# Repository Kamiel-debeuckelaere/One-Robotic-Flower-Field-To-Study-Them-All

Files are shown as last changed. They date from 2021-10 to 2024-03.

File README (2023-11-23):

Dear visitor

In this repository you can find several folders, each containing different information and files to construct robotic flowers.
- 3D-design files
- Firmware to put on the arduino (only use one of the two included .cpp files!)
- Node-RED flows
- PCB-design files
- Proof of concept, with data, script and video

We bundled a lot of information in the user manual, including instructions for construction and use of the robotic flower. 
I hope you can find everything you need, if not, don't hesitate to ask!

Kind regards

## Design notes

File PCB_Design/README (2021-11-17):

This folder contains files to obtain Gerber files that are needed for PCB fabrication. 
Open these files in EasyEDA online.

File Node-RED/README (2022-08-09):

This directory contains 2 flows in JSON format that can be imported in Node-RED.
More information on how to import a flow: https://nodered.org/docs/user-guide/editor/workspace/import-export

These flows construct the dashboard website (see figure) and construct the CSV files of incoming data.

It is necessary to add the following modules to the palette:
- node-red-contrib-fs
- node-red-dashboard
- node-red-node-tail

The 'File Logger Flow' is only needed once per robotic flower field system.
-> change path to folder where CSV should be stored (nodes: 'filename generator', 'file-lister', 'init' and 'reset')

The 'Flower Flow' is needed for every separate robotic flower in the system
-> change topic so it contains the right device and app name!
-> update server security settings in downlink and uplink node for each flower
-> create dashboard website tabs (Battery, Alarms, Sleep time, Refill gap and Files) and groups for each flower
-> next, assign the following nodes per flower to the right tab and group, an example for flower 1:
    - Received: '[Alarms] Flower1' 
    - Received: '[Battery] Flower1' 
    - Chart:'[Battery] Flower1' 
    - Gauge: '[Battery] Flower1' 
    - Queue is full: '[Alarms] Flower1' 
    - Send during visit: '[Alarms] Flower1' 
    - Battery warning: '[Alarms] Flower1' 
    - Possible obstruction: '[Alarms] Flower1'
    - Refill gap: '[Refill gap] Flower1' 
    - Going to sleep at: '[Sleep time] Flower1'
    - Waking up at: '[Sleep time] Flower1' 

Screenshots of dashboard website
The user interface of the frontend application with the different tabs opened. 
For example, in the 'battery' tab an overview of all the robotic flowers in use can be seen with the time of the last update (last received message), 
the battery voltage, and a graph of the voltage decline in function of time.

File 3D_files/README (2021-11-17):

This directory contains a Zip-compressed archive file for Autodesk® Fusion 360® (.f3z) and a folder with stl-files of the prototype ready for 3D-printing.

To open the archive file, select "Upload" in the Fusion 360 Data panel and choose the F3Z file. 
The contents of the file will be loaded in Fusion 360, displaying the main assembly in the panel with the F3D design(s), allowing you to view and edit them.

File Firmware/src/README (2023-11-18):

In this folder, there are 4 possible sourcefiles containing a slightly different program. 

!! you can only use one source file at once, so delete the ones you don't need before opening the 'firmware' folder in e.g., Visual Studio Code !!
 
 1) 'main.cpp' has automatic refilling and a refill gap (that can be chosen from the NodeRed dashboard website) after a visit,
     keep in mind you have to slect a refill gap in orde to have the flower working properly!
 
 2) 'main_autoRefillOnly.cpp' only has the automatic refilling (that can be chosen from the NodeRed dashboard website)

 3) 'main_no_sending.cpp' can be selected if you want to use the robotic flower for refilling only

 4) 'main_RFID_no_RX_sending.cpp' can be selected when you combine the flowers with the Microsensys RFID system.
     The RFID radio waves will make the flowers deaf, meaning they cannot receive instructions anymore, so in this firmware version,
     when the flower is put to sleep, it will keep sending data but not expecting an answer. Note that you will have to put the
     flowers to sleep from the dashboard website before switching on the RFID readers.

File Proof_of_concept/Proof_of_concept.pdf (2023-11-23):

# Proof of concept

## Contents

## 1. First tests

A proof of concept was performed to test whether the robotic flower does what it was designed to do. Multiple insects in different settings were used on July 16, 2021. The question was if the robotic flowers could attract visitors by offering artificial nectar and if so, correctly register the visit data. Therefore, the CSV-file with visit data of the robotic flower had to be compared to the manually collected visit time and visit duration. Two robotic flowers were used of which the nectar reservoir was filled with Biogluc (50% w/w) sugar syrup (composed of 25.0% sucrose, 37.5% fructose, 34.5% dextrose, 2.0% maltose, 1% higher sugars and 0.05% preservatives) made by Biobest (Billiet et al., 2016).

## 1.1 Open Field

As a first setting, the robotic flower was placed in the garden. Floral visitors were recorded in an open field setting, being a small botanical garden. When the visitor went in the feeding hole, the probing time and duration were noted (table 1). The captured individuals were identified and besides Bombus terrestris, also B. pascuorum, Anthidium manicatum, Apis mellifera, Psythirus sp., Syrphidae, Bombyliidae and even one Lepidopteran showed interest in the robotic flower (at least to a certain extent). After manually registering visits, we compared this to the data collected by the robotic flower. 7 out of the 10 visitors that actually went in the feeding hole to drink were recorded by the robotic flower, but we noticed that some visits were not or only partly recorded (See table 1). In retrospect, this could be partly explained by the ‘SENSOR_SENSITIVITY’ value that was used. The sensitivity of the IR detection system, that was set at a good value for the breadboard prototype, might have been insufficient sensitive in the garden conditions, especially for the smaller floral visitors. For butterflies, with their long proboscis, a more refined feeding hole would probably be needed to get sufficient blocking of the infrared sensor.

2

## Table 1

Manual measurement | Robotic Flower | Analysis Robotic Flower system
Species | Class | Remarks

Visit Time
(hh:mm)

Visit
Duration (s)

Visit Time
(hh:mm:ss)

Visit
Duration (s) Visit registration | Percentage time
1 | Syrphidae | Fly | | 13:33 | 8 | | | x
2 | Bombus pascuorum | Bee | male | 13:45 | 5 | | | x
3 | Bombyliidae | Fly | | 14:08 | 240 | 14:08:49 | 78 | Yes | 33%
4 | Lepidoptera | Butterfly | | 14:13 | 158 | | | x
5 | Bombus pascuorum | Bee | didn’t drink | 14:19
6 | Syrphidae | Fly | didn’t drink | 14:22
7 | Anthidium manicatum | Bee | | 14:59 | | 14:59:17 | 2 | Yes
8 | Bombyliidae | Fly | didn’t drink | 15:11
9 | Apis mellifera | Bee | didn’t drink | 15:23
10 | Apis mellifera | Bee | 2nd visit by same bee | 15:39 | 35 | 15:39:23 | 26 | Yes | 74%
11 | Apis mellifera | Bee | 3th visit by same bee | 15:39 | 10 | 15:40:01 | 14 | Yes | 140%
12 | Apis mellifera | Bee | | 15:49 | 8 | 15:49:20 | 3 | Yes | 38%
13 | Bombus terrestris | Bee | | 15:51 | 148 | 15:51:26 | 52 | Yes | 35%
14 | Bombus terrestris | Bee | male | 15:56 | 9 | 15:57:20 | 9 | Yes | 100%

## 2.1 Greenhouse

The second setting was in the greenhouse with the robotic flower placed inside a small flight cage (60 × 60 × 60 cm; front and back in clear vinyl, right and left in polyester netting mesh, Bugdorm, Megaview Ltd.; Fig. 1) together with lab-reared floral visitors from Biobest (Westerlo, Belgium). Two species were tested in separate trials: bumble bees (Bombus terrestris), and Eupeodes corollae (a common European species of Syrphidae). After a training period, both speciesshowed great interest in the robotic flower, making it sometimes hard to visually discriminate multiple visits. That is most likely why the results of the manual data collection often show only one visit where the robotic flower recorded multiple visits (Table 2). All visits detected manually were also present in the data sent by the robotic flower.

The robotic flower has a visit time accurate to the second while the manual registration only had minutes, but the visit times seem to match perfectly, as can be seen in Table 2. The ‘duration overlap’ gives a view on the difference between manual and the robotic measurement of the visit duration (the separate robotic flower timings added together and divided by the manual timing). This was close to 100% in many cases, and the deviations can be explained in different ways. A duration overlap is different from 100% could be the effect of multiple visits that were measured by the robotic flower compared to one large visit in the manual censuses. The small gaps in between these visits can explain the difference in visit duration. For example, in visit 5 in the flight cage setup (Table 2), the manual measurement shows one long visit of 77 seconds, while the robotic flower registered five different visits of 9, 5, 4, 12 and 27 seconds. The total of the three separate visits gives a duration of 57 seconds, which means a duration overlap of 74%. When looking closer to the intervals between those visits, we see gaps of 2, 5, 1 and 12 seconds. Taking these
gaps into account, the result is a duration of
77 seconds and thus a duration overlap of
100%. In visits with a small duration, the duration overlap can drastically deviate from the target value of 100% because of manual registration bias. Starting or stopping the timer a fraction later or earlier and rounding errors by the observer has a big impact if the visit duration was only a couple of seconds. For example, visit 19 (Table 2) had a manual measured duration of only 2 seconds, while the robotic flower registered 3 seconds. Only one second difference in this case leads to a duration overlap percentage of 150%.

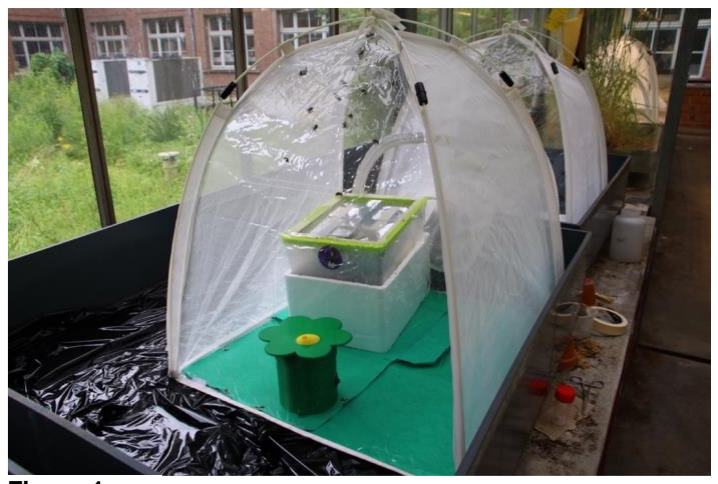
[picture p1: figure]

Looking critically at the results of the analysis of the robotic flower, it can be concluded that the detection of visits works as it should, provided that the IR sensitivity is set to the right value for the setup. A calibration is thus recommended before starting an experiment using the robotic flowers. This proof of concept also showed that not only bumble bees but also many other floral visitors can be investigated even with the same hardware parts. In the set-up with the flight cage, we had satisfactory results for the syrphids E. corollae although it is advisable to reduce the diameter of the feeding hole specifically to better match their body size.

Figure 1

4

## Table 2

Manual Measurement | Robotic Flower | Analysis Robotic Flower system
Species | Visit Time (hh:mm) | Visit Duration (s) | Visit Time (hh:mm:ss) | Visit Duration (s) | Visit registration | Duration overlap (%)
B. terrestris | 15:18 | 128 | 15:18:16 | 51 | Yes | 98%
| | | 15:19:09 | 52
| | | 15:20:02 | 23
B. terrestris | 15:21 | 27 | 15:21:06 | 20 | Yes | 96%
| | | 15:21:38 | 6
B. terrestris | 15:22 | 67 | 15:22:04 | 3 | Yes | 93%
| | | 15:22:09 | 1
| | | 15:22:12 | 58
B. terrestris | 15:23 | 56 | 15:23:17 | 10 | Yes | 66%
| | | 15:23:30 | 12
| | | 15:23:51 | 15
B. terrestris | 15:24 | 77 | 15:24:09 | 9 | Yes | 74%
| | | 15:24:20 | 5
| | | 15:24:30 | 4
| | | 15:24:35 | 12

5

15:24:59 | 27
B. terrestris | 15:28 | 39 | 15:28:03 | 27 | Yes | 82%
| | | 15:28:39 | 5
B. terrestris | 15:33 | 26 | 15:33:54 | 22 | Yes | 104%
| | | 15:34:18 | 5
B. terrestris | 15:35 | 23 | 15:35:09 | 25 | Yes | 109%
B. terrestris | 15:35 | 9 | 15:35:48 | 3 | Yes | 33%
B. terrestris | 15:35 | 29 | 15:35:56 | 21 | Yes | 72%
B. terrestris | 15:37 | 13 | 15:37:03 | 9 | Yes | 69%
B. terrestris | 15:37 | 5 | 15:37:22 | 14 | Yes | 280%
B. terrestris | 15:37 | 14 | 15:37:44 | 12 | Yes | 100%
| | | 15:37:58 | 2
B. terrestris | 15:42 | 46 | 15:42:11 | 39 | Yes | 98%
| | | 15:42:52 | 6
B. terrestris | 15:43 | 7 | 15:43:05 | 30 | Yes | 125%
B. terrestris | 15:43 | 17
B. terrestris | 15:43 | 31 | 15:43:38 | 8 | Yes | 90%
| | | 15:43:48 | 2

6

15:43:56 | 18
B. terrestris | 15:44 | 47 | 15:44:49 | 37 | Yes | 79%
B. terrestris | 15:45 | 2 | 15:45:30 | 3 | Yes | 150%
B. terrestris | 15:46 | 5 | 15:46:00 | 1 | Yes | 140%
| | | 15:46:15 | 6
B. terrestris | 15:47 | 10 | 15:47:04 | 38 | Yes | 127%
B. terrestris | 15:47 | 20
E. corollae | 15:56 | 75 | 15:56:15 | 3 | Yes | 85%
| | | 15:56:53 | 13
| | | 15:57:41 | 30
| | | 15:58:17 | 18
E. corollae | 15:59 | 175 | 15:58:43 | 190 | Yes | 109%

## 2. Foraging-preference experiment

To further prove the value of this new robotic flower, we performed a bumblebee foraging-preference experiment with two reward qualities in a greenhouse setting. After training on less rewarding flowers, we expect an initial preference for these lower-quality flowers (flower constancy) with a gradual shift towards the higher quality option during the trial (Heinrich, 1981). To test this, a robotic flower field consisting of 16 robotic flowers, alternating less and more rewarding flowers in a 4x4 setup, was used in two subsequent replicate trials (Fig. 2). The two types of flowers are represented by different colours, yellow and blue, so that foragers can discriminate between them visually and associate them with reward quality (Hammer & Menzel, 1995). We used Biogluc 30% w/w (less rewarding) and 60% w/w (more rewarding) as artificial nectar with preservatives to reduce microbial growth (Billiet et al., 2016). For both trials, a 7-weeks old lab-reared B. terrestris colony was placed in the arena with the robotic flowers. Before a trial, colonies were fed pollen and Biogluc ad libitum directly in the nest, but Biogluc supply was ceased 24 hours in advance to stimulate foraging. A trial started with 36 hours of training, where the colony was placed in a closed bug dorm with two 30% w/w rewarding flowers (without refilling gap). Subsequently, the bug dorm was opened at night to allow foraging in the arena starting the next morning. A refill gap of 30 minutes was implemented during this experimental phase.

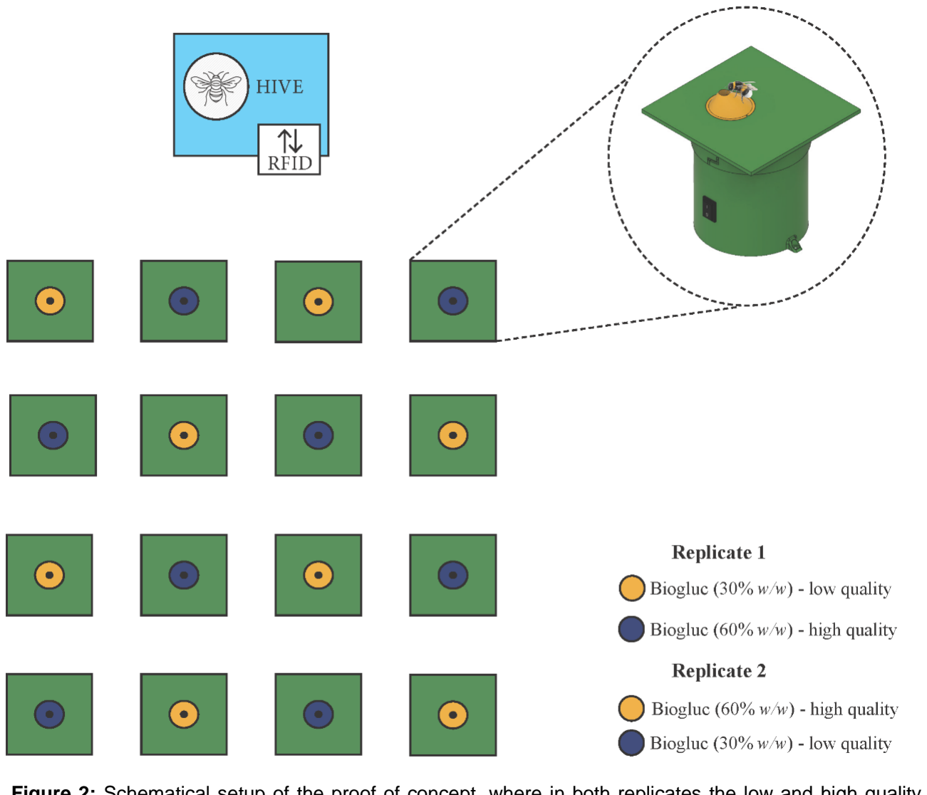
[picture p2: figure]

Figure 2: Schematical setup of the proof of concept, where in both replicates the low and high quality sources were switched between the yellow and blue flower.

In total, 70 177 visits were recorded in this proof of concept. During the daily inspection of the setup within peak activity time-slots, a maximum of five foragers at once were observed. with the earliest flower visit at 7:36 and the latest at 19:17, the natural light regime (sunrise ~7:55, sunset ~19:00) was well visible.

The data were analysed using R version 4.2.1 (R Core Team, 2022). A heatmap representing the number of visits per flower per treatment (Fig. 3) already indicates an initial preference for the low concentration flowers with a switch towards the high concentration during the experiment.

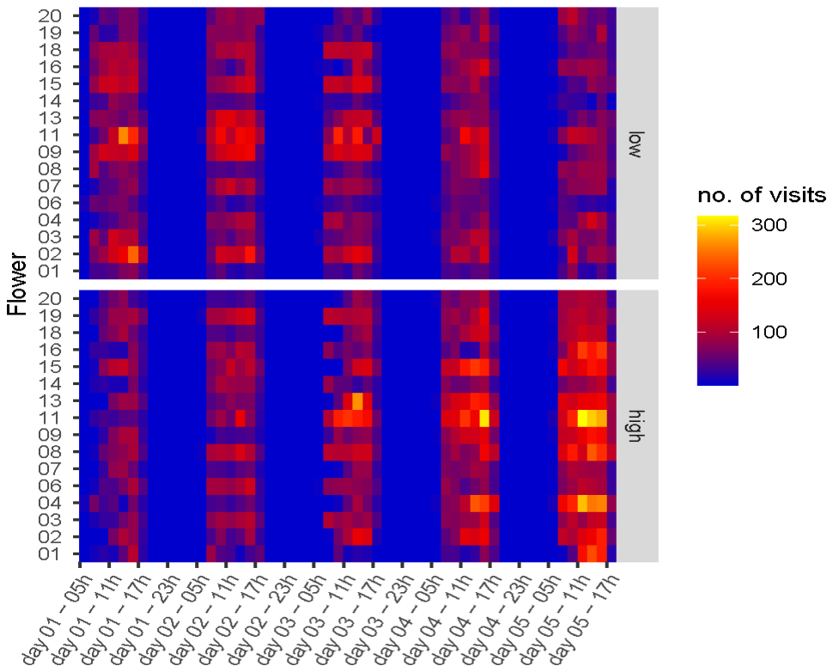
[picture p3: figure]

Data on the number of visits per hour per flower (n) were used in a general linear mixed model with Poisson distribution and an observation level random factor to account for overdispersion:

fit = glmer(n ~ (1|flower) + concentration * scale(exp_day) +

mSpline(hour_of_day, df=7, Boundary.knots = c(0,24), periodic=TRUE) + (1|obs),

family = poisson (link="log"), data = model_data,

control = glmerControl(optimizer = "Nelder_Mead", optCtrl = list(maxfun=100000)))

Figure 3: A heatmap of the number of flower visits per quality of the nectar reward over the experimental period.

As can be seen in the Anova table (table 3), the model gives a significant effect of experimental day (p = 0.00039), as well as a significant interaction between the Biogluc concentration and experimental day (p < 2.2e⁻¹⁶). A significant effect was also found for the circadian rhythm in foraging (p < 2.2e⁻¹⁶).

In the first day after being trained on the low concentration, bumblebees visit the low concentration flowers about double as much as they visit high concentration flowers (high/low contrast ratio = 0.525, p < 0.0001). There is a linear trend of increasingly more visits towards the high concentration compared to the low concentration (high/low contrast estimate = 0.338, p < 0.0001), resulting in no significant difference in visitation rate between the two concentrations on the third experimental day (high/low contrast ratio = 1.032, p = 0.2765). On the last experimental day, the preference has switched to little over double the amount of visits to high concentration flowers compared to the low concentration flowers (high/low contrast ratio = 2.030, p < 0.0001). The effect plot (Fig. 4) gives a clear view on this preference shift, including the circadian rhythm in foraging.

Table 3: Anova

Predictor | Chisq | Df | P value
Intercept | 47.28744 | 1 | 6.13E-12 ***
Concentration | 1.184415 | 1 | 0.276
Experimental day | 12.57797 | 1 | 0.00039 ***
Hour of day | 3205.677 | 7 | < 2.2E-16 ***
Conc. : Exp. Day | 265.8984 | 1 | < 2.2E-16 ***

Table 4: Estimated marginal means of linear trends (emtrends)

Contrast | Estimate | SE | P value
High/Low | 0.338 | 0.0207 | < 0.0001 ***

Table 5: Estimated marginal means (emmeans)

Contrast | Day | Ratio | SE | P value
High/Low | 1 | 0.525 | 0.0270 | < 0.0001 ***
High/Low | 2 | 0.736 | 0.0268 | < 0.0001 ***
High/Low | 3 | 1.032 | 0.0303 | 0.2765
High/Low | 4 | 1.448 | 0.0514 | < 0.0001 ***
High/Low | 5 | 2.030 | 0.1019 | < 0.0001 ***

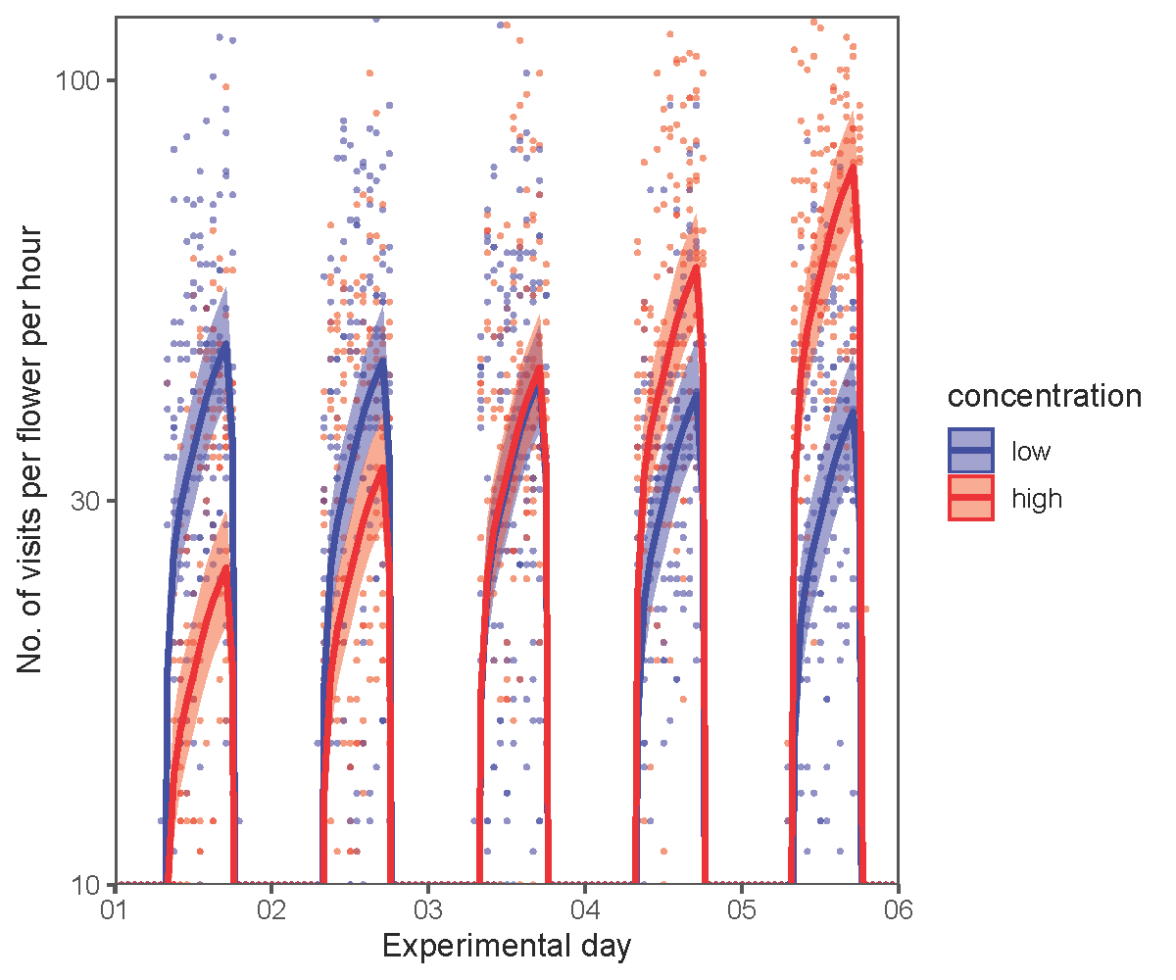
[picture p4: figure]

## 3. Waterproof testing

A robotic flower was put outside in rainy conditions (November 2023) to see if the system can withstand the water (Fig. 5). For this test, we used the roofed central flower disk design to prevent water entering the feeding hole. To make sure the flower bottom is not soaked completely in the wet underground, we elevated it slightly from the ground. To prevent tipping over by the wind or uncareful by passers (e.g. nosy birds), the flower was anchored in the ground.

The flower kept working as long as the battery was charged and did not show any signs of leakage, which proved the system’s water resistance.

Figure 4: An effect plot of the number of bumblebee flower visits per concentration as predicted by the generalized linear mixed model plotted over the raw data.

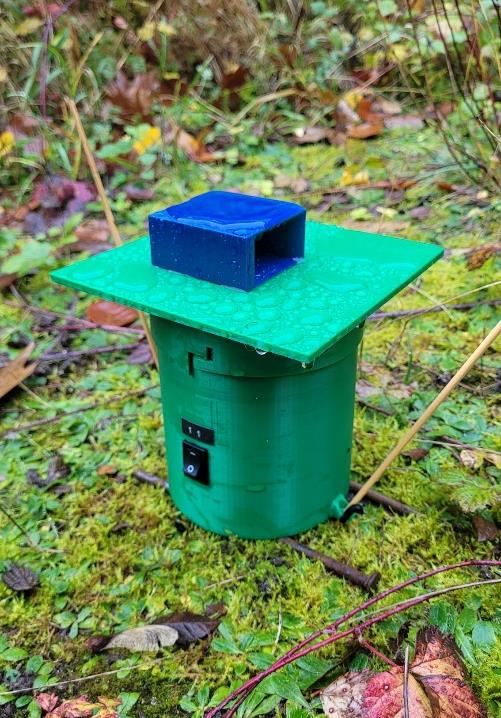
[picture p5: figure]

Figure 5: a robotic flower placed outside in the rain, anchored in the ground.

## 4. References

Billiet, A., Meeus, I., Van Nieuwerburgh, F., Deforce, D., Wackers, F., & Smagghe, G. (2016). Impact of sugar syrup and pollen diet on the bacterial diversity in the gut of indoor-reared bumblebees (Bombus terrestris). Apidologie, 47(4), 548-560. https://doi.org/10.1007/s13592-015-0399-1

Hammer, M., & Menzel, R. (1995). Learning and memory in the honeybee. The Journal of Neuroscience, 15(3), 1617-1630. https://doi.org/10.1523/jneurosci.15-03-01617.1995

Heinrich, B. (1981). Bumblebee economics (3 ed.). Harvard University Press.

R Core Team. (2022). R: A language and environment for statistical computing. In R Foundation for Statistical Computing. https://www.R-project.org/

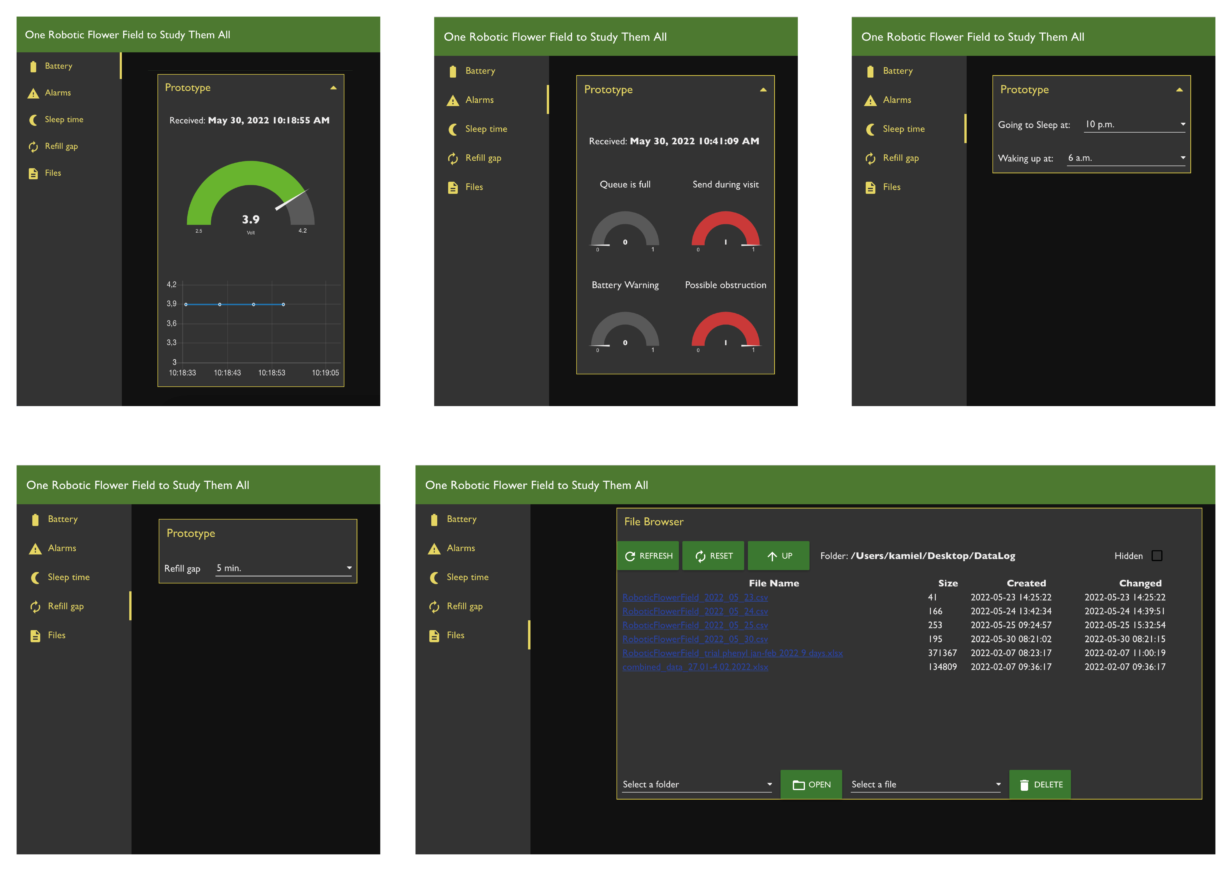
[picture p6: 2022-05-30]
Node-RED/dashboard view 2.png

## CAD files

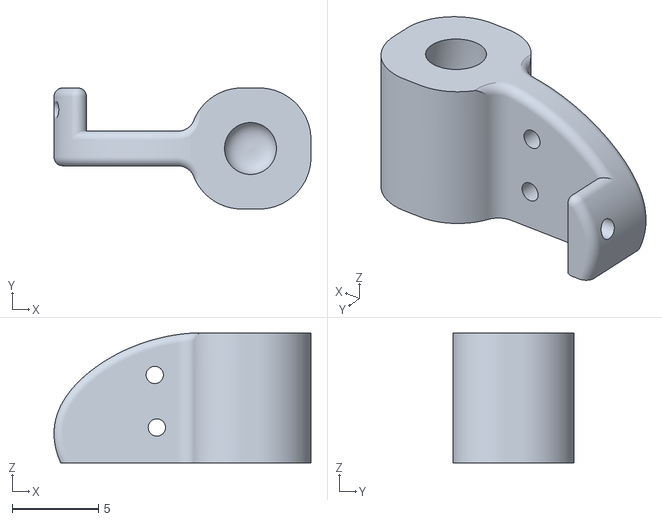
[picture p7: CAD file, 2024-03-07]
3D_files/Robotic_Flower_STL/Nectar cup 2 - 15 µL.stl
14.9 x 7.00 x 7.50

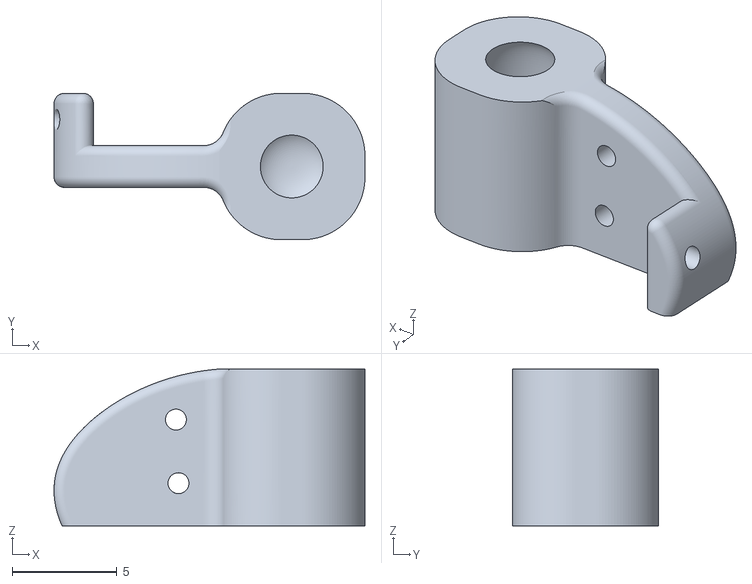
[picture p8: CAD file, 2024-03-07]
3D_files/Robotic_Flower_STL/Nectar cup 1 - 22 µL.stl
14.9 x 7.00 x 7.50

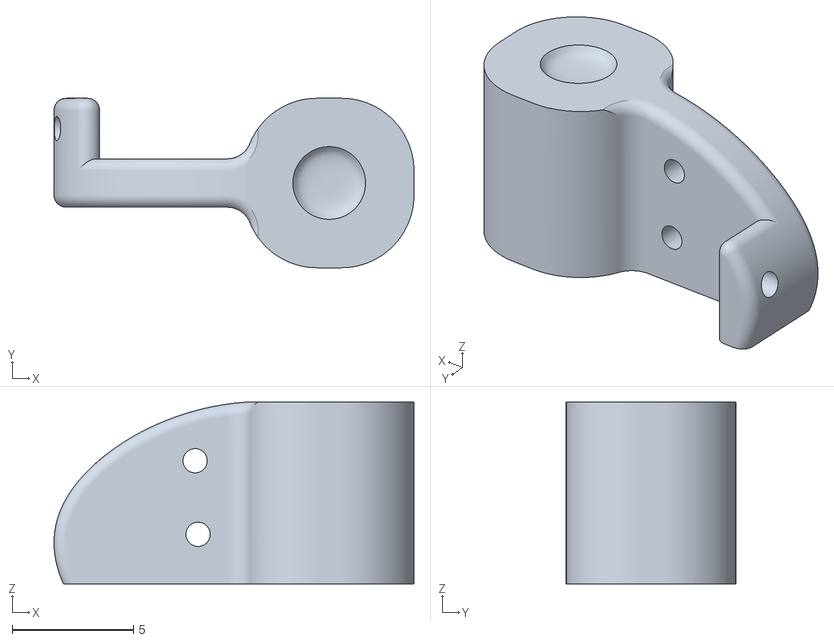
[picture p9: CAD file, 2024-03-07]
3D_files/Robotic_Flower_STL/Nectar cup 5 - 6.4 µL.stl
14.9 x 7.00 x 7.50

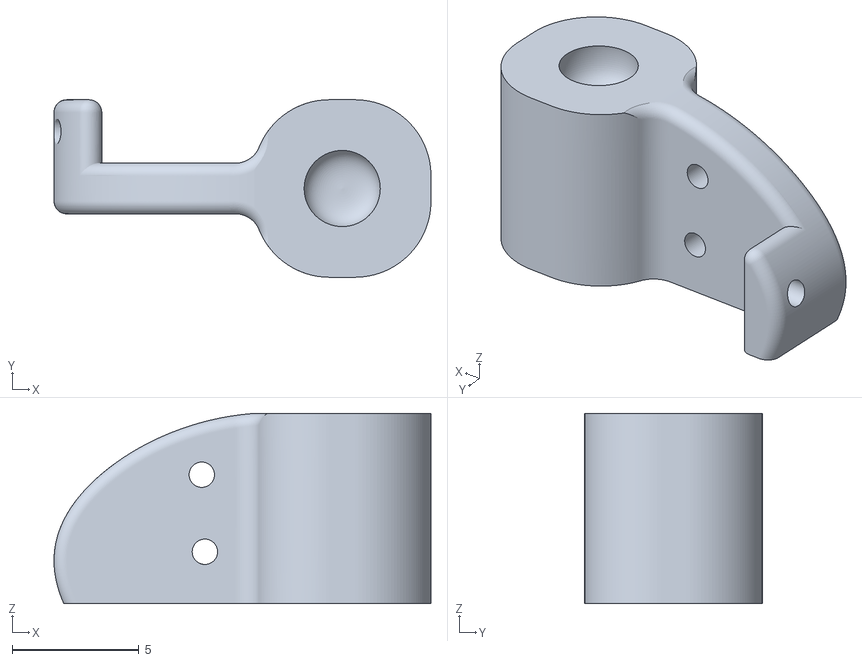
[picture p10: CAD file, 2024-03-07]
3D_files/Robotic_Flower_STL/Nectar cup 3 - 12 µL.stl
14.9 x 7.00 x 7.50

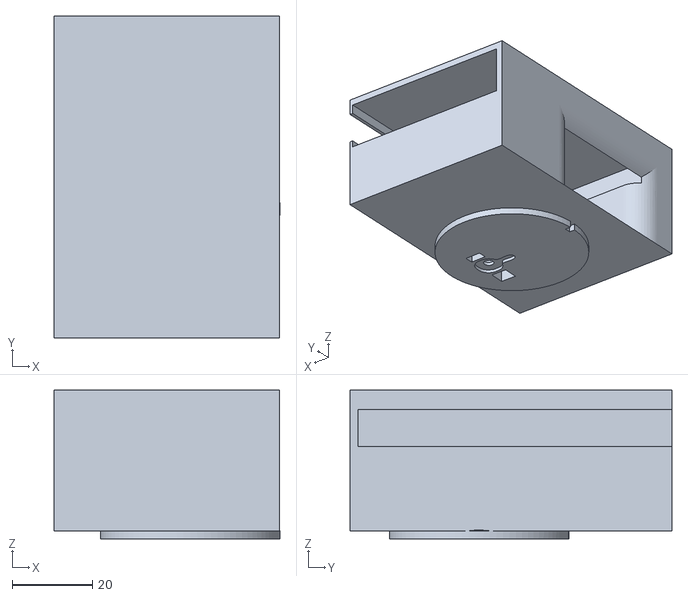
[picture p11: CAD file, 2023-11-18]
3D_files/Robotic_Flower_STL/Central flower disk - RFID.stl
56.2 x 80.0 x 37.0

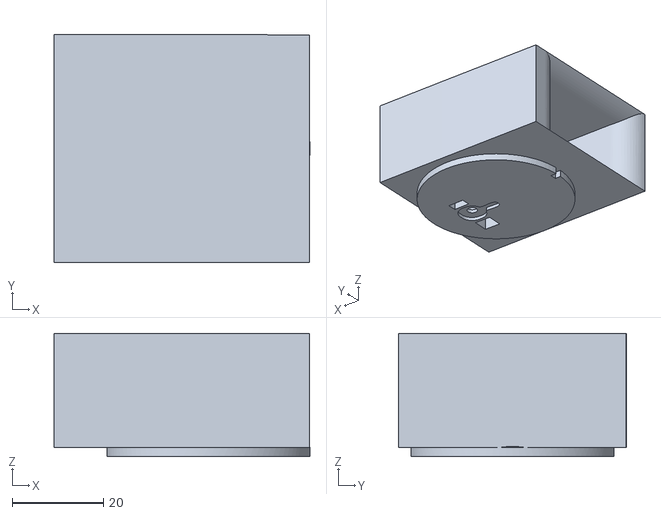
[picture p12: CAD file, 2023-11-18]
3D_files/Robotic_Flower_STL/Central flower disk - roof.stl
56.2 x 50.0 x 27.0

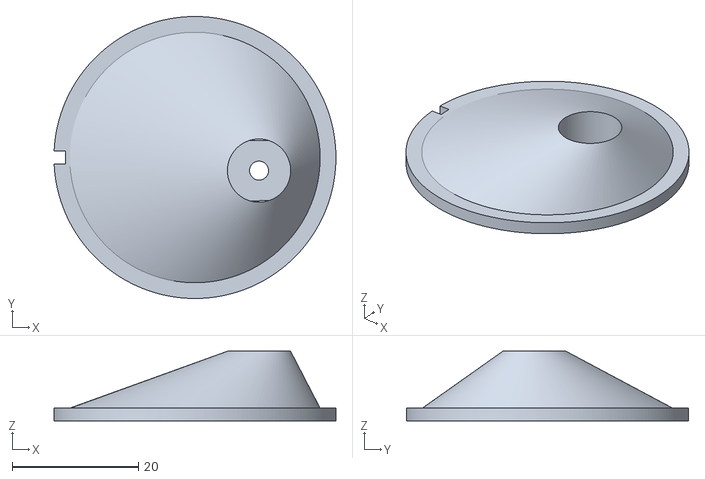
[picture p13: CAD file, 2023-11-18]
3D_files/Robotic_Flower_STL/Central flower disk - standard.stl
44.6 x 44.6 x 11.0

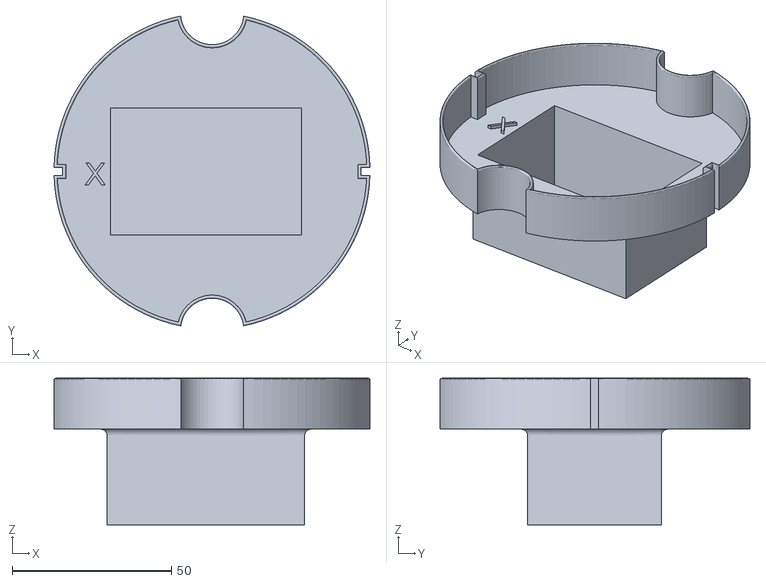
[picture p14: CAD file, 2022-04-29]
3D_files/Robotic_Flower_STL/Reservoir Case (black).stl
99.2 x 97.2 x 46.0

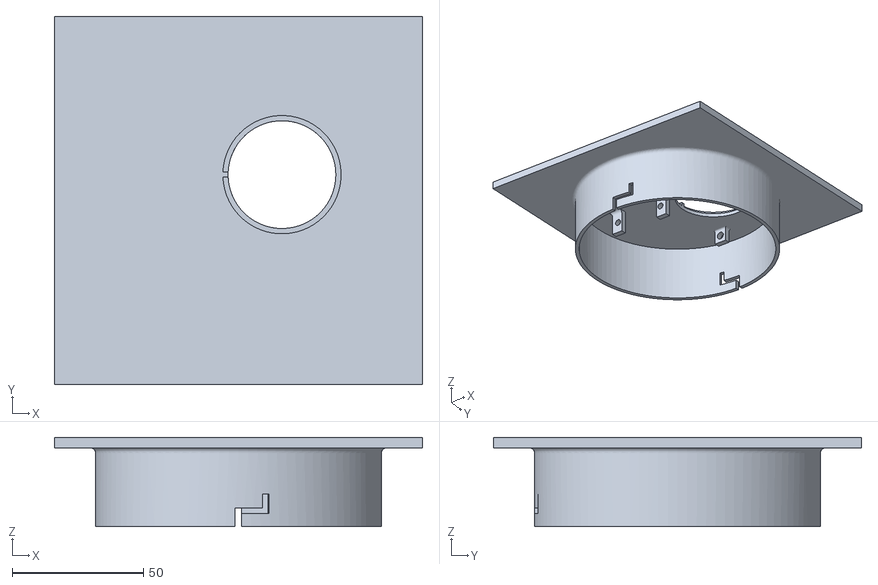
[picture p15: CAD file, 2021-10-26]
3D_files/Robotic_Flower_STL/Background Plane (green).stl
140.0 x 140.0 x 34.0

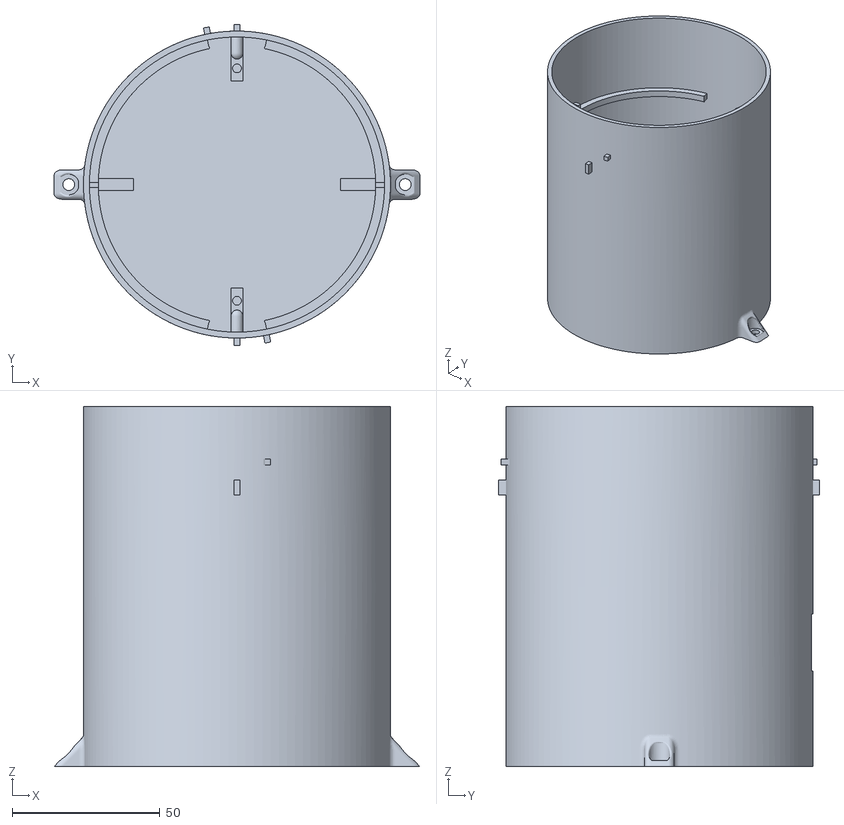
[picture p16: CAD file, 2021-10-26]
3D_files/Robotic_Flower_STL/Stem (green).stl
124.0 x 108.8 x 122.0

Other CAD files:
3D_files/Robotic_Flower_STL/Nectar cup 6 - 4.5 µL.stl
3D_files/Robotic_Flower_STL/Nectar cup 4 - 8.5 µL.stl
3D_files/Flower 4 v9.f3z
3D_files/Flower 7 v13_Microsensys_RFID_integration.f3z

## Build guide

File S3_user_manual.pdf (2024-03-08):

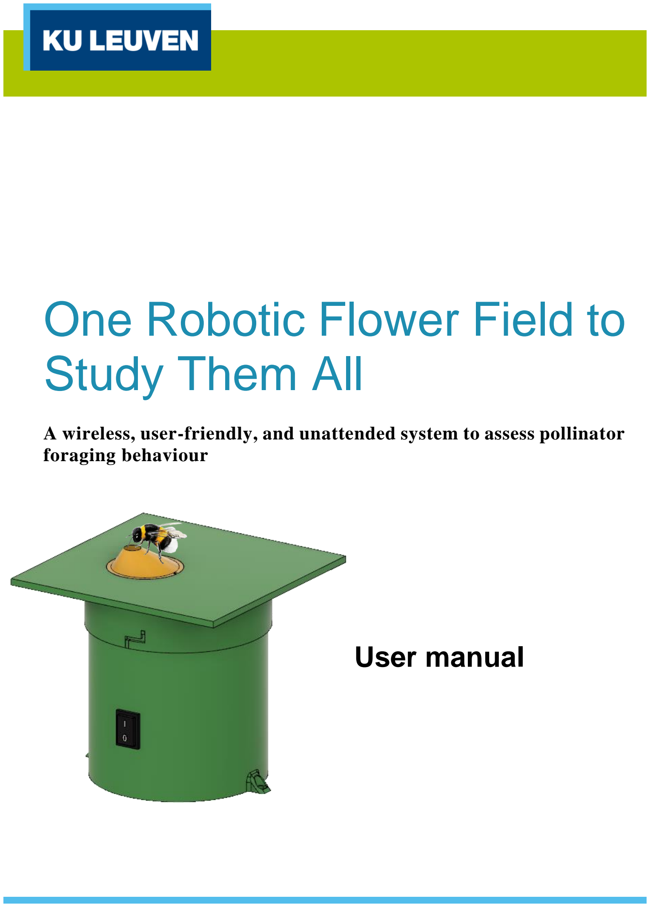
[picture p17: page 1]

# One Robotic Flower Field to Study Them All

## A wireless, user-friendly, and unattended system to assess pollinator foraging behaviour

# User manual

## TABLE OF CONTENTS

## 1 INTRODUCTION

Assembling the flower(s), creating your own Node-Red dashboard, uploading the firmware to the Arduino… It sounds like a lot of work, but by making this guide we aim to help you to get this done before you know it. You will have to make sure everything works as it is supposed to before the final step: preparing the experimental set-up. We will try to lead you through this process and give some tips that can save some trouble when using this robotic flower system. And in the end, our only hope is that the robotic flowers will prove very helpful in gathering the data that you want!

As a first step, you have to go to the GitHub repository: https://github.com/Kamiel-debeuckelaere/One-Robotic-Flower-Field-To-Study-Them-All (https://github.com/Kamiel-debeuckelaere/One-Robotic-Flower-Field-To-Study-Them-All) . In there, you can download a zip-folder containing all documents to build this robotic flower by clicking on the green button saying ‘Code’ (Fig. 0). Keep the structure with subfolders and save it to an accessible part of your computer (so that it is easy to access afterwards). These subfolders will be used for different parts in this user manual.

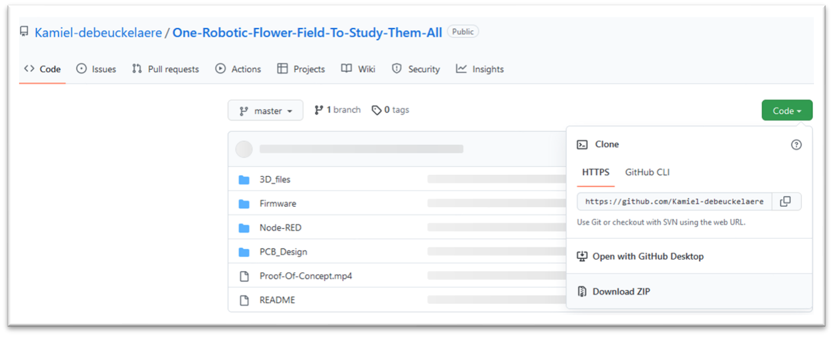
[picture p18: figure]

Figure 0

## 2 ROBOTIC FLOWER CONSTRUCTION

Make sure you have all materials that are needed to construct the robotic flowers. In the parts list (appendix 1) you can find every item that is needed. You can also find the store and the link to the product we have used, but alternatives are possible. Also make sure you have all the necessary tools to complete the construction, or at least have access to them (e.g., soldering station, 3D-printer, electrical screwdriver etc.).

## 2.1 PCB

- To print the PCB, you will need the Gerber files of the design. To get these, the .json files on GitHub must be opened with the online (and free) software EasyEDA, after creating an account. The PCB’s can be ordered directly through this website as well.
- EasyEDA: https://easyeda.com/
- When PCB’s have arrived, carefully solder all the needed parts to the PCB. To do this, see electrical scheme (appendix 2). We started with the through hole parts (ordered from small to large parts for practical reasons during soldering) and ended with the surface mounted LoRa module (rn2483a). A useful tip might be to use a stereomicroscope to solder the relatively fine connections of this LoRa module, as any wrong connection will lead to malfunction. The soldering of the LoRa module is a precision job and can be a bit of a challenge, but it is possible!
- For normal use with battery, connect the bottom two pads of solder jumper SJ1 with tin. In this way, power from the battery is directed to the power switch. When you want to use the flowers connected to the power grid with power coming from the micro-USB on the microcontroller, the top 2 pads must be connected with tin.
- Here, we use a 5V PWM servomotor, meaning solder jumper SJ2 can be ignored. When working with a 3.3V PWM servomotor, SJ2 needs to be connected.

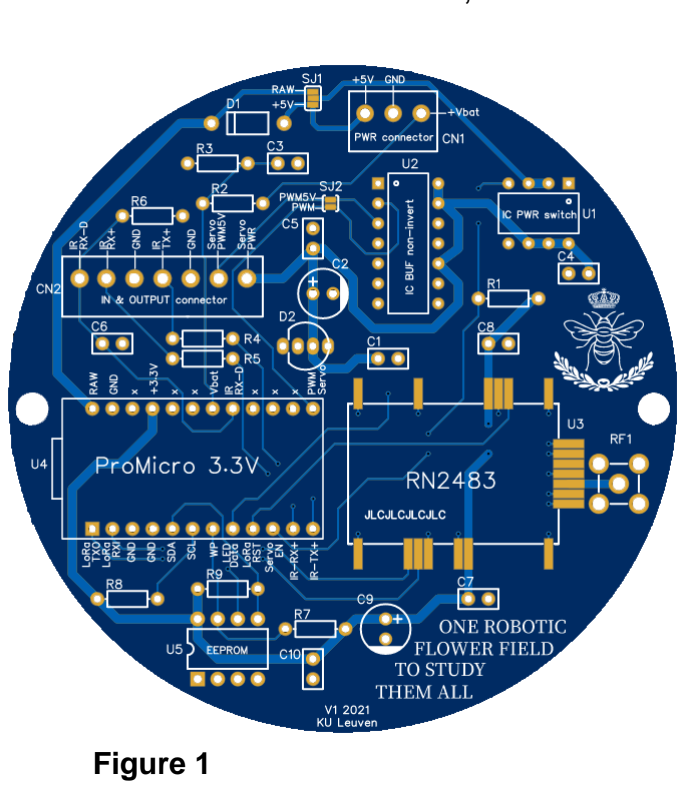
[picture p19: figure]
Figure 1
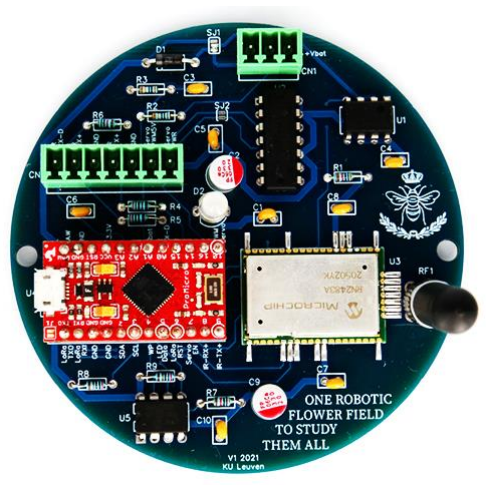
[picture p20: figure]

2.2 BATTERY MODULE

- Solder the connector to the battery module board and plug in the cables going to the rocker switch. The rocker switch itself can be connected later (see Fig. 3).
- Attach a wire (we used 25 cm) to one of the cables (cut and solder together) going to the rocker switch. This is to let the Arduino read the battery voltage. To cover the part of the cable where now the insulation (plastic cover) is missing, you can use heat-shrink tubing (see Fig. 2).
- Solder wires (positive + and negative -) to the UPS (uninterrupted power source) output of the board. Make sure these wires are long enough (we used 20 cm).
- Solder the board to the battery holder with through-hole soldering and make sure the + and – side are correct
- The clip-in part of the module was originally designed for flat-top batteries but was here manually modified with pincers to fit the button-top battery we selected. If used with flat-top batteries, no modification would be needed.
- Connect the +, - and voltage reader at the correct place to the power connector (term block) using a small screwdriver. This way, the wires can be plugged into to the PCB later.

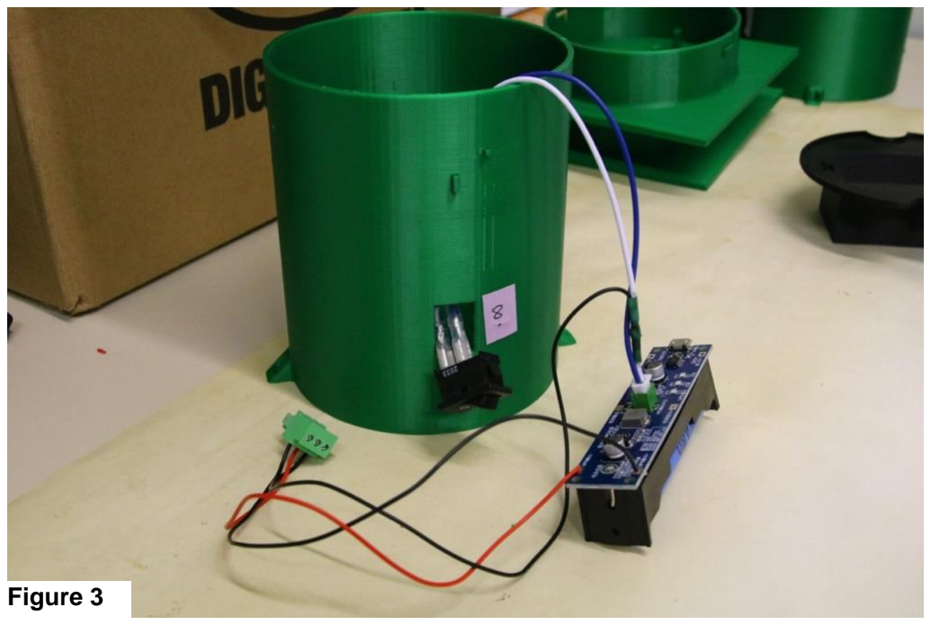
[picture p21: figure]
Figure 3

2.3 3D-PRINTING & ASSEMBLY

The STL files for 3D printing can be found in GitHub (https://github.com/Kamiel-debeuckelaere/One-Robotic-Flower-Field-To-Study-Them-All/tree/master/3D_files). (https://github.com/Kamiel-debeuckelaere/One-Robotic-Flower-Field-To-Study-Them-All/tree/master/3D_files) If you wish to modify parts, you can
download | and | install | Autodesk | Fusion | 360 | (https://www.autodesk.com/products/fusion-
360/overview?term=1-YEAR&tab=subscription), (https://www.autodesk.com/products/fusion-360/overview?term=1-YEAR&tab=subscription) a 3D designing software which has a free hobby version and a free educational version (for qualifying students and teachers). In this program, you can then upload the zip compressed archive file (.f3z) and start editing. Moreover, many tutorials on how to use this software can be found online.

The robotic flower has 5 3D-printed parts: central flower disk (Fig. 4, A), nectar cup (Fig. 4, B), background plane (Fig. 4, C), reservoir case (Fig. 4, D) and the stem (Fig. 4, E). After printing, first carefully remove the support structures (the most parts can be done manually, but for smaller edges e.g., by using a needle nose plier or a scalpel), and make sure there is no hindering for assembly anymore. Dimensions of the robotic flower can be seen in Fig. 5. We recommend watching also the short assembly animation movie that can be found on GitHub.

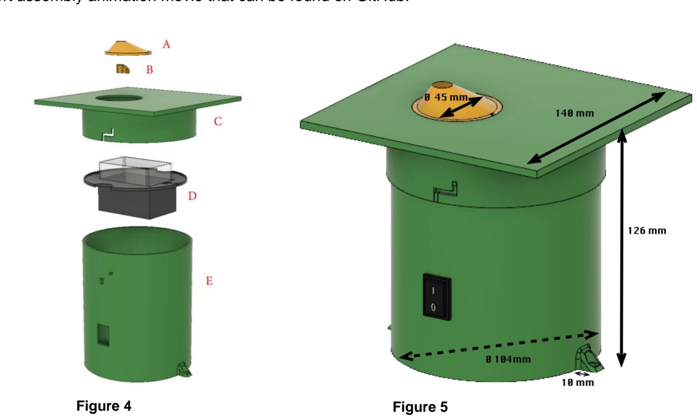
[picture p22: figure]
Figure 4; Figure 5

### 2.3.1 STEM

- At the bottom, four beams (Fig. 6, B) are in place to support the PCB so that it is elevated from the bottom. This was done to prevent the PCB being in contact with water when condensation is formed in the flower and runs down the sides. A slit between the wall and PCB is kept free so that the condensation can run to the bottom. To keep the PCB in place, two of the four supports have cylindrical protrusions that fit the holes of the PCB.
- On top of the PCB, there is space left to place the battery module with battery. This design with a broad stem, in which the battery is not put upright, ensures a low centre of gravity, helping to avoid easy tipping over of the robotic flower.
- The stem has two support beams (Fig. 6, A), one at each side to hold up the nectar reservoir case (see further). Two protrusions are provided which fit the notches in the reservoir case to prevent it from moving around. Keeping the right position is important for the well-functioning of the servo refilling system.

- In the side of the stem there is a hole (Fig. 6, C) to fit in the on/off switch that can be clipped in.
- Protrusions for the twist-and-lock system (Fig. 6, D) to fit the background plane on top of the stem which keeps the components from disconnecting easily.
- The mounting feet (Fig. 6, E) are constructed to fix the robotic flower on the substrate to keep it from tipping over if necessary. For example, the flower could be anchored in the ground using a small picket, or it could be screwed onto a platform.

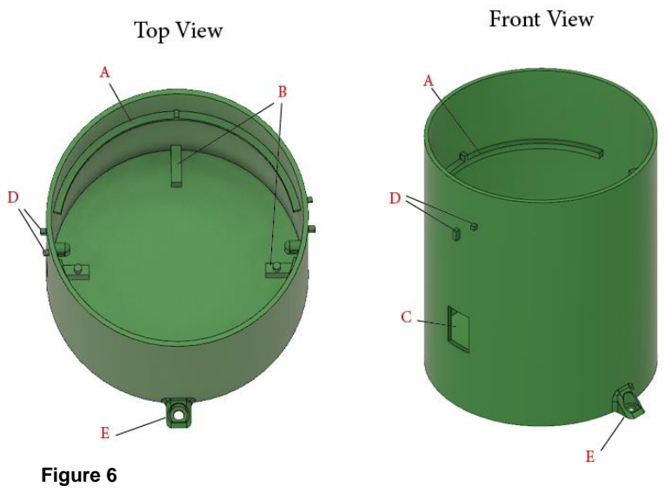
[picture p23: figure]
Figure 6

2.3.2 BACKGROUND PLANE AND CENTRAL FLOWER DISK
- The background plane is constructed so that it fits over the stem and is kept in place with a twist-and-lock system for which notches are present on the side (Fig. 7.2, A).
- On the bottom of the background plane two protrusions with holes are constructed (Fig. 7.2, B) to attach the servomotor (Fig. 7.2, C) with zip ties (2.5 x 200 mm).
- In the place where the central flower disk must fit, an opening with a ledge is made. In this ledge, a protrusion is constructed in such a way that the central flower disk (Fig. 7.2, D) with notch can be placed in the right position before being fixated with transparent silicone. In this way, the seal is also made waterproof.

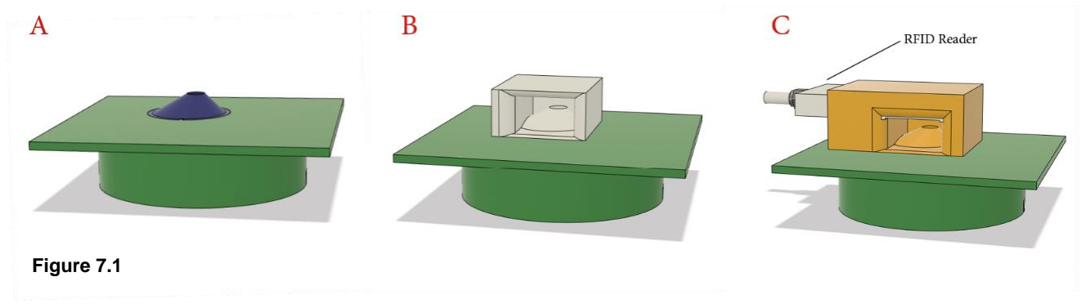
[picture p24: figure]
Figure 7.1

- The central flower disk can come in different shapes and colours (see Fig. 7.1 for the ones we already provided). The conical shape of the central flower disk (Fig. 7.1, A) is to avoid rain running off from the background plane in the feeding hole as much as possible, but the shape surrounding the feeding hole can be changed. A more waterproof design, with a roof, is available (Fig. 7.1, B), or a shape to combine the system with RFID readers (here from Microsensys, Fig. 7.1, C).
- In the central flower disk, a cylindrical hole is constructed through which pollinators can enter the flower to reach the nectar. The feeding hole can thus not be too small for the large workers to be able to enter it. Still, in contrast to the 13 mm in the previous version of Kuusela & Lämsä (2016), we chose a smaller diameter for the feeding hole in this new robotic flower. Based on experience by Pozo et al. (2020) that showed a mean Bombus terrestris worker thorax width of 6.97 ± 0.85 mm we chose to make the feeding hole 10 mm in diameter to reduce the interference of external light (e.g., from the sun) with the infrared sensor while still leaving enough space for the workers to enter.
- The depth of the feeding hole should be deep enough so that visitors are forced to crawl inside to reach the nectar and thereby causing a disturbance in the infrared barrier of the detection system. With the average length of B. terrestris workers being 14.1 ± 2.4 mm (personal communication with Biobest, Westerlo, Belgium), the depth of the feeding hole was chosen to be 9 mm.
- The infrared (IR) emitter and sensor both have a positive and negative pole, which are soldered with one wire each (black for – and red for +; we used a wire-length of 40 mm) and covered with heat-shrink tubing. The IR emitter and sensor are then glued in the two designated holes in the central flower disk (Fig. 7.2, E; Fig. 8) with transparent silicone. The 4 wires coming from the from the IR emitter and sensor are kept together with heat-shrink tubing and are attached to the term block together with the 3 wires coming from the servomotor.
- At the bottom of the feeding hole (Fig. 7.2, F), there is a nectar hole with a diameter of 3 mm and depth of 1 mm through which floral visitors can reach the nectar cup that is pressed against the central flower disk by the servomotor. A notch shaped like the nectar cup is made at the bottom of the central flower disk to ensure a tight fit and a correct position of the nectar cup relative to the central flower disk.
- Other structures are protrusions with holes to guide the cables coming from the infrared emitter and sensor so that they don’t hinder the servo-arm during refilling (Fig. 7.2, G).

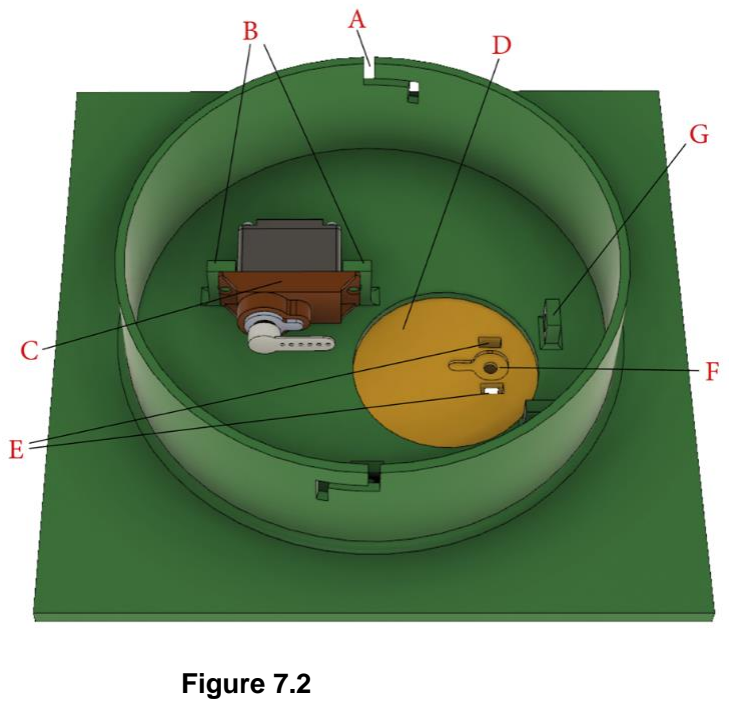
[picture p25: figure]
Figure 7.2
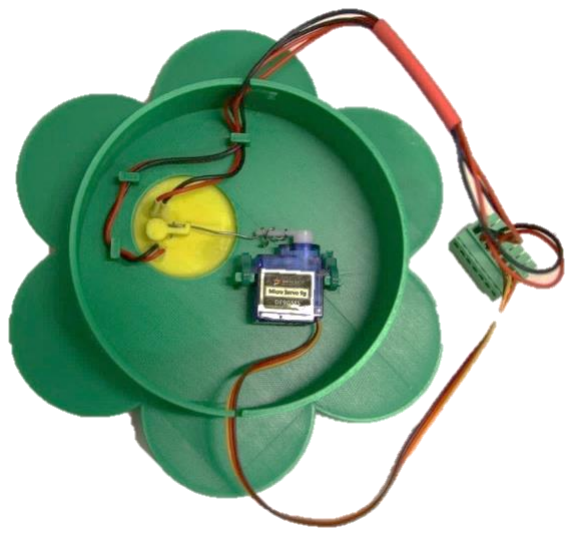
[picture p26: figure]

Figure 8

2.3.3 NECTAR CUP
- By changing the 3D-design of the nectar cup, it is easy to adapt the discrete volume of the nectar presented to visitors of the robotic flower according to specific needs. For this prototype version, the volume is approximately 15µL (see repeated measurements with capillary tubes in ‘6 Nectar cup volume’.
- Another characteristic to consider here is the length of the proboscis of visitors, this because they need to be able to reach the bottom part of the nectar cup. The proboscis length varies among species and is an ecological important factor in assessing which species have access to floral rewards. The hole in this nectar cup (Fig. 9, A) has a diameter of 3 mm (to match the hole in the central flower disk) and depth of 3.5 mm. The thickness of the central flower disk at the point where it meets the nectar cup is 1 mm. This distance must be added to the depth of the hole in the nectar cup, making a total depth of 4.5 mm. This is easily reachable for B. terrestris (and B. lucorum) workers with a functional proboscis length of 8.1 ± 0.2 mm, Apis mellifera workers with 6.6 ± 032 mm and B. pascuorum workers with 8.9 ± 0.2 mm (Balfour et al., 2013). The proboscis length of Lepidoptera in a study with 15 species by Corbet (2000) also showed to be sufficient to reach the nectar in the robotic flower, ranging from 7.34 ± 0.07 mm for Lycaena phlaeas to 16.19 ± 0.41 mm for Inachis io. Most Syrphinae (Diptera) have a proboscis that is relatively short related to their size, but some species, including Eupeodes corollae and Platycheirus manicatus have a longer proboscis (3-5 mm) (Branquart & Hemptinne, 2000). For these syrphids, the nectar cup might be too deep to reach all the way to the bottom, but during the proof of concept this did not seem to stop them from visiting the robotic flower.
- The nectar cup has three holes (Fig. 9, B) through which the part
of the servo-arm, consisting of steel wire (diameter 0.8 mm), can
be attached. The other end of the servo-arm is clipped on the spindle of the servomotor. Because the servo-arm partly consists of steel wire, it can be manipulated manually to achieve a close fit between the nectar cup and the central flower disk, so that both holes are matching (see Fig. 8). More information in part ‘7.2 Attaching servo arm’.

2.3.4 RESERVOIR CASE
- The reservoir case is built to carry the nectar reservoir (Fig. 10,
E) while also forming a protective barrier between the electronic components at the bottom and the artificial nectar located at the top.
- The case is supported by beams on the stem and is kept in the right position by notches (Fig. 10, B) that fit in protrusions of these
beams.

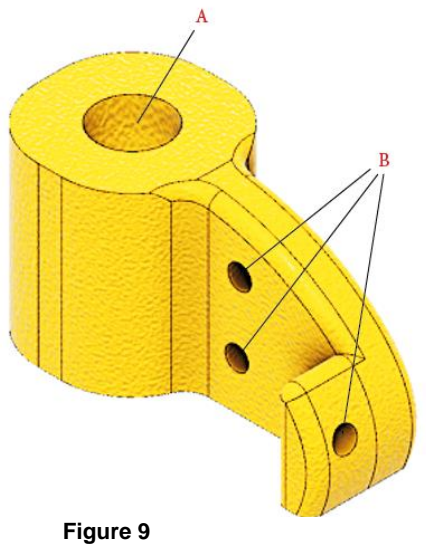
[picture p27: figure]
Figure 9

- Crescent notches (Fig. 10, C) at both sides of the nectar reservoir case ensure a passage for the cables from the servomotor, infrared sensor and emitter attached to the bottom of the background plane running towards the electronics compartment at the bottom of the stem.
- A rim (Fig. 10, D) is provided on the edge of the reservoir case to prevent spill-over nectar from the nectar reservoir to seep into the electronics compartment underneath. In the latest updated version of the 3D-design, these edges have been made higher than is seen in Fig. 10.

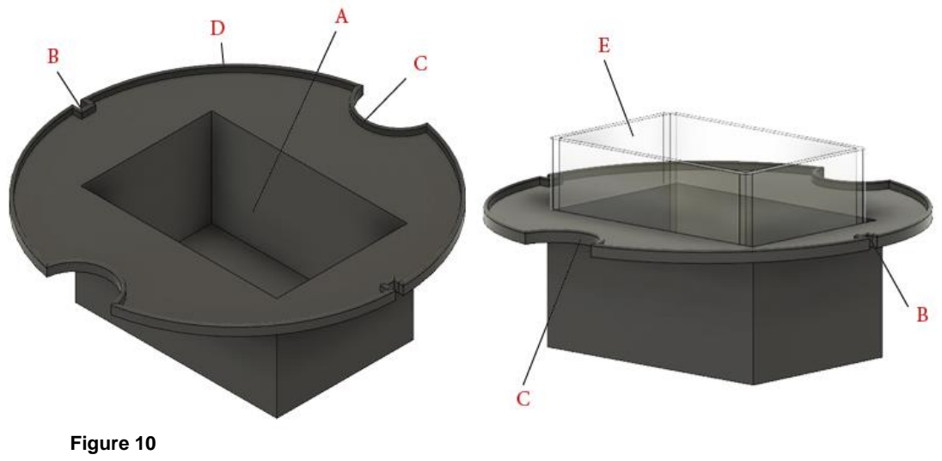
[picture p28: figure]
Figure 10

2.3.5 NECTAR RESERVOIR
- For this prototype an off-the-shelf reservoir with inside dimensions of 56 × 36 × 44 mm (L × B ×
H) was used, giving it a volume of 88.7 ml (Fig. 10, E).
- In a hypothetical set-up with a nectar cup of 25 μL that is depleted every time, a standard refilling rate of 10 minutes and in working mode for 14 hours every day, the robotic flower would theoretically be capable of offering nectar for more than 40 days. This is when the nectar reservoir is filled up completely to the edge, ignoring spill-over and evaporation and assuming the servo-refilling system can scoop all the nectar down to the last drop. This is not a realistic scenario, but it shows that there is enough margin for an experimental set-up of e.g., two weeks. (With long experimental periods other problems will probably arise, such as uncontrolled bacterial growth in the artificial nectar.)
- If another size is wanted, a nectar container could also be custom made, with the restriction that also the nectar reservoir case will have to be modified and keeping in mind that the servo-arm must fit in the reservoir when refilling.

## 3 SETUP IOT

To work with Internet of Things, you will need a LoRaWAN backend and one ore multiple gateways, depending on the specific application. If you are lucky, you might use a pre-existing LoRaWAN communication infrastructure provided by your university or institute (as we did). We recommend you to inquire about this at your ICT service.

If no such service is available to you (yet), it is still possible to get a gateway yourself and use ‘The Things Network’, which provides a free LoRaWAN backend infrastructure globally. More information can be found here: https://www.thethingsnetwork.org/

You will have to make an application (choose unique name) first. Here you can create/generate an AppEUI (EUI stands for ‘Extended Unique Identifier’) and an AppKey. Both these numbers will be needed later in step ‘6.5 Initializing the flower’.

In this step you should also find your API security key that will be needed in your Node-RED downlink and uplink security settings (see part 4 ‘Node-RED’).

For now, that’s all you can do. Later you will have to add all your devices (a.k.a. robotic flowers) with their Device EUI (DevEUI) in the application you created. This DevEUI is the unique number defining each LoRa module and can be found by reading it out, but we will come back to this in step ‘6.5 Initializing the flower’. You will have to create unique names, e.g. flower1, flower2… A tip is to write these names/numbers on the LoRa module or somewhere else on the PCB.

Note that the frequency plan for the radio communication is region bound, e.g. we used Europe 863-870 MHz.

# 4 NODE-RED

Node-Red is a browser based editor needed to receive all the data and creating the daily csv-file on one hand, and on the other hand to generates the dashboard website to monitor all robotic flowers in use. With this programming tool we created a flow of connected JavaScript functions making up the application consisting of a backend and a frontend. The backend receives data from the LoRaWAN backend, processes them and provides them to the frontend application (Node-RED dashboard). The backend also stores the visitation data in a daily CSV-file (an example can be found in supporting information of the paper). For every visit, a new line is added in the file containing the time at the start of the visit, duration of the visit and the name of the device that registered the visit (e.g., ‘flower 1’). That

is why it is very important to keep Node-RED running continuously when the robotic flowers are in use! If not, data might be lost.

To get started, you need to install Node-RED. For this, there are multiple options (see website of Node-RED: https://nodered.org/ ). You can use a local computer, a device like a Raspberry Pi or have it running in the cloud. We used a computer to run Node-RED locally. Just note that this computer will need to stay running as long as an experiment is running as Node-RED is responsible for all communication from and to the flowers. Different guidelines for installation can be found on the Node-RED website.

Figure 11

After installing on your local machine, you can run Node-RED from the ‘Terminal’ (macOS) or ‘Command Prompt’ (Windows) by typing: ‘node-red’ (Fig. 11). Node-RED will start running and then you can use the displayed server address to go to the web interface. Once you are in the flow editor, you will need get nodes and connections between the nodes in there to build the flows. The program consists of two parts, one for file logging and one for communication with all the robotic flowers separately. These two parts are available in the folder you downloaded from GitHub. Both files are in JSON-format ready to be imported in Node-RED. More information on how to import a flow: https://nodered.org/docs/userguide/editor/workspace/import-export. (https://nodered.org/docs/user-guide/editor/workspace/import-export)

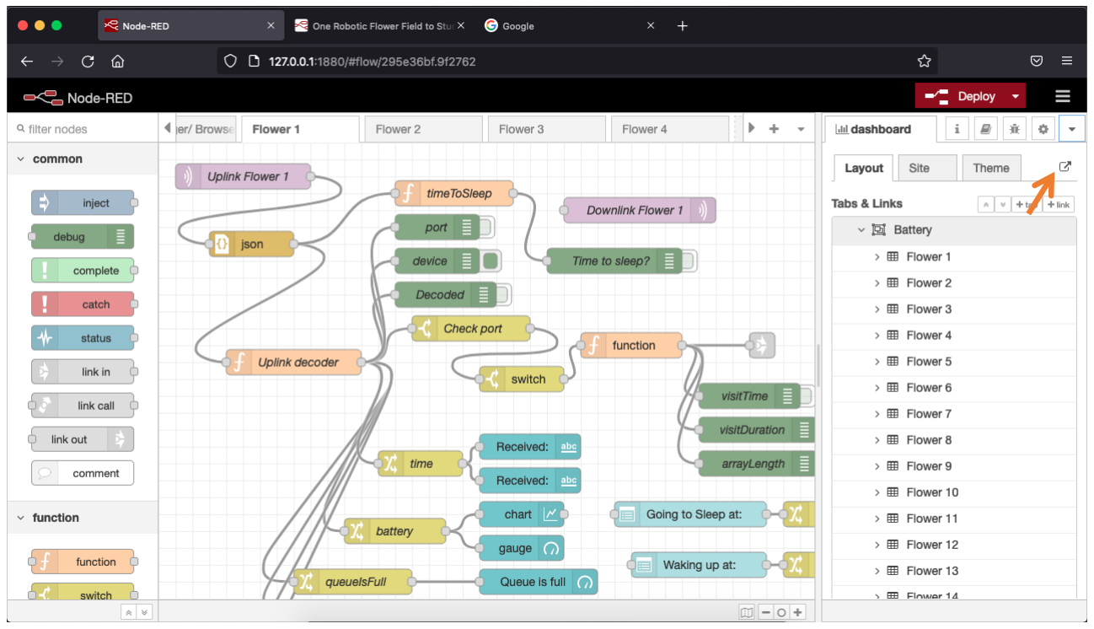
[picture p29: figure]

If you never used Nod-RED before or don’t have the necessary modules installed, you will need to add the following modules to the palette:

- node-red-contrib-fs
- node-red-dashboard
- node-red-node-tail
1. The 'File Logger Flow' is only needed once per robotic flower field system. Here you need to change the path to where you want a new subfolder ‘DataLog’ created where your CSV-files will be stored. The nodes where you need to do this are:
- 'filename generator'
- 'file-lister'
- 'init'
- 'reset'
2. The 'Flower Flow' is needed for every separate robotic flower in the system. So, for example, if you want to use 4 flowers, you will need to import this flow in 4 different tabs (Fig. 12). Also here, you will need to do some important changes for every flower in the Uplink and Downlink nodes:
- change name and topic so it contains the right device and app name!
- update server security settings in downlink and uplink node for each flower

Figure 12

So far so good. Now it is time to structure your dashboard website. You can play around with it of course and arrange it as you see fit, but we will show you how we did it (Fig. 13). First go to the dashboard page, opening it on the left side of your screen as can be seen in Fig.12. There, we created the different tabs for the dashboard: Battery, Alarms, Sleep time, Refill gap and Files. Next, in each tab except ‘Files’, we made a group for each flower.

We constructed the dashboard in such a way that, for example, the 'battery' tab shows an overview of all the robotic flowers that are in use with the time of the last update (last received message), the battery voltage, and a graph of the voltage decline in function of time. We assigned the the necessary nodes per flower to the right tab and group, an example for flower 1 given below:

- Received: '[Alarms] Flower1'
- Received: '[Battery] Flower1'
- Chart:'[Battery] Flower1'
- Gauge: '[Battery] Flower1'
- Queue is full: '[Alarms] Flower1'
- Send during visit: '[Alarms] Flower1'
- Battery warning: '[Alarms] Flower1'
- Possible obstruction: '[Alarms] Flower1'
- Refill gap: '[Refill gap] Flower1'
- Going to sleep at: '[Sleep time] Flower1'
- Waking up at: '[Sleep time] Flower1'

One can also see the benefit of having a Tab for each flower (e.g., could be useful for use on smartphone), but here we like the quick overview of all the flowers in one tab.

To see the dashboard website you just created, click on the little link symbol in the top (Fig. 12, arrow). In ‘Theme’ you can later customize colours, titles etc. of your dashboard website.

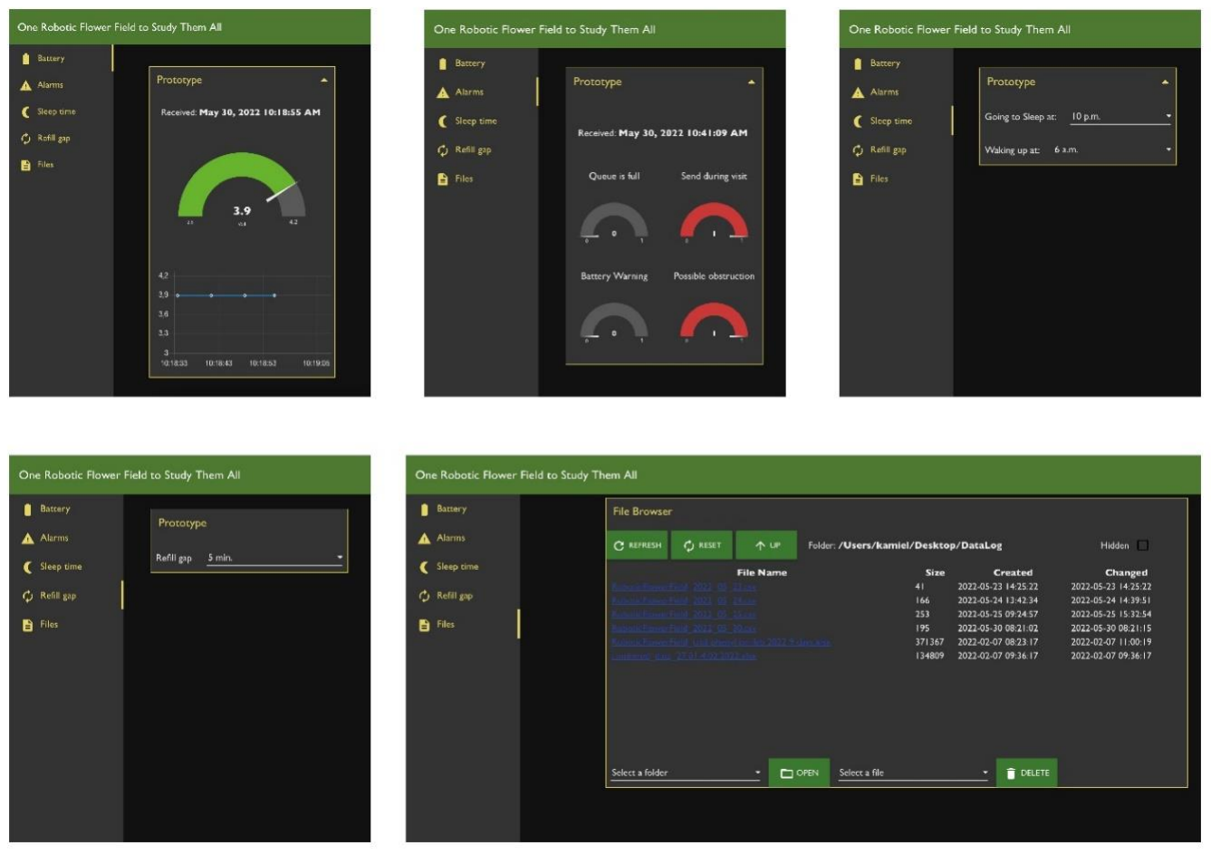
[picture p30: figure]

Figure 13

## 5 UPLOADING FIRMWARE TO ARDUINO

5.1 SOFTWARE INSTALLING

To be able to see, edit and upload the firmware, a code editing software is needed. We used Visual Studio Code (VSC) as it is a free program that is built on open source and offers great flexibility. You are of course welcome to use whatever other editor you might have experience with.

To get started, you will need to download Visual Studio Code from https://code.visualstudio.com/

Next, you can install PlatformIO from the extension list when you have opened the freshly installed VSC (Fig. 14). PlatformIO is an integrated development environment (IDE) that we have experienced as very well suited for this kind of project. You can also already install C/C++ extension pack, or do it later when VSC prompts you to do so.

5.2 DOWNLOAD FIRMWARE

Remember the folder you saved before from GitHub? Now, we will need to do some stuff there before continuing. In the folder ‘Firmware’, you can find the subfolder ‘src’ in which different files can be found each containing a slightly different version of the firmware controlling the robotic flower. Before you can proceed to the next steps, you will have to remove one of both out of the firmware folder as you can only use one of both at once.

Choose the firmware file best suited for your needs:

1) 'main.cpp' has automatic refilling and a refill with refill gap (that can be chosen from the Node-RED dashboard website) after each visit. E.g., on top of the automatic refilling every 10 minutes (or other time specified when uploading the firmware) to prevent drying out, the flower will also refill after a bee visits (leaving a gap time that can be chosen remotely).
2) 'main_autoRefillOnly.cpp' only has the automatic refilling (that can be chosen from the Node-RED dashboard website remotely)
3) ‘main_no_sending.cpp’ can be selected if you want to use the robotic flower for refilling only.
4) 'main_RFID_no_RX_sending.cpp' can be selected when you combine the flowers with the Microsensys RFID system (see part ‘9 Combining with RFID system from Microsensys GmbH’).

Now you can open the firmware folder using VSC. Once you opened the files in the editor, you can use the explorer on the right of the screen (Fig. 14) to see all the files.

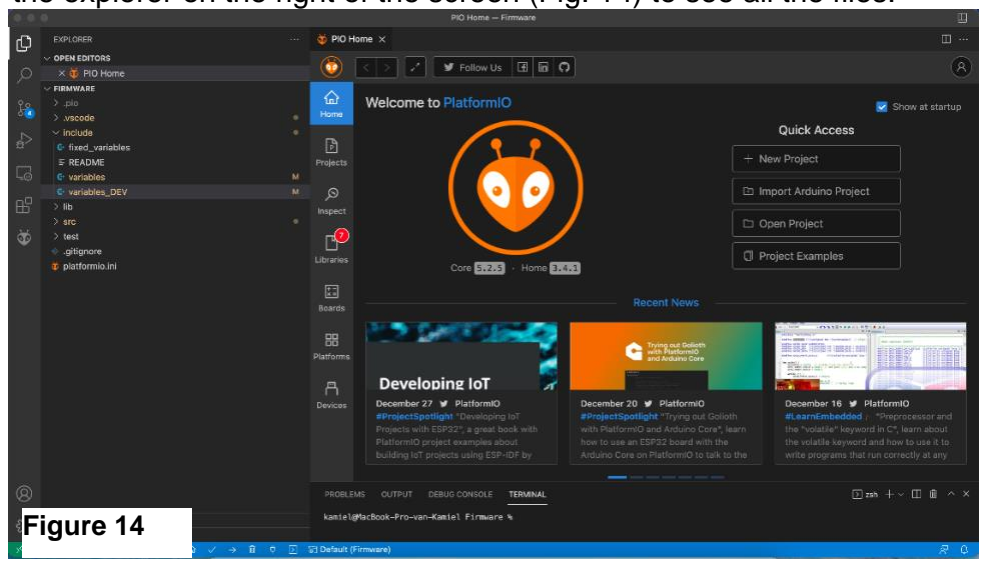
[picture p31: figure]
Figure 14

5.3 MODIFY FIRMWARE TO FIT NEEDS

If you want to change parameters so they fit your exact research questions, you can open the file ‘variables’ in the folder ‘include’. Here you can find all the parameters with some explanation and easily change them before uploading to the Arduino (Fig. 15).

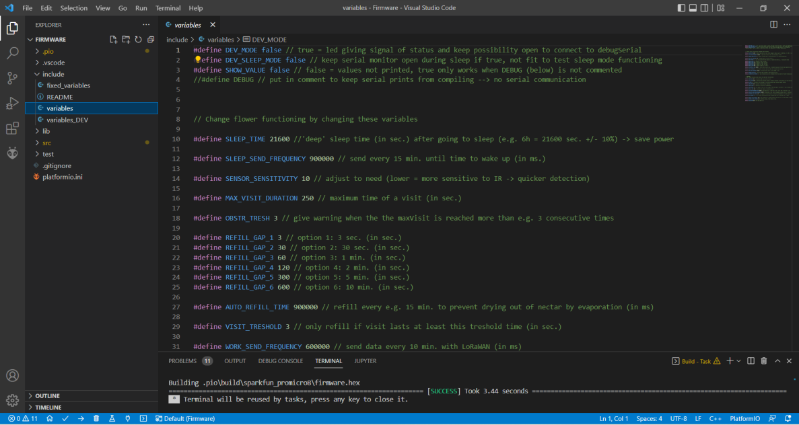
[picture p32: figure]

5.3.1 LIST OF ADJUSTABLE PARAMETERS

- SLEEP_TIME 21600 // 'deep' sleep time (in sec.) after going to sleep (e.g. 6h = 21600 sec. +/- 10%) -> save power
- SLEEP_SEND_FREQUENCY 900000 // send every 15 min. until time to wake up (in ms.)
- SENSOR_SENSITIVITY 10 // adjust to need (lower = more sensitive to IR -> quicker detection)
- MAX_VISIT_DURATION 250 // maximum time of a visit (in sec.)
- OBSTR_TRESH 3 // give warning when the the maxVisit is reached more than e.g. 3 consecutive times
- REFILL_GAP_1 3 // option 1: 3 sec. (in sec.)
- REFILL_GAP_2 30 // option 2: 30 sec. (in sec.)
- REFILL_GAP_3 60 // option 3: 1 min. (in sec.)
- REFILL_GAP_4 120 // option 4: 2 min. (in sec.)
- REFILL_GAP_5 300 // option 5: 5 min. (in sec.)
- REFILL_GAP_6 600 // option 6: 10 min. (in sec.)
- AUTO_REFILL_TIME 900000 // refill every e.g. 15 min. to prevent drying out of nectar by evaporation (in ms)
- VISIT_TRESHOLD 3 // only refill if visit lasts at least this treshold time (in sec.)
- WORK_SEND_FREQUENCY 600000 // send data every 10 min. with LoRaWAN (in ms)
- WARNING_VOLTAGE 3 // give alarm when voltage is lower than this value
- RECONNECTION_TRESHOLD 2 // LoRa reconnection will be attempted after this amount of failed transmissions

Figure 15

5.4 UPLOAD TO ARDUINO

Now you are ready to upload the firmware to your Arduino Pro Micro. To do that, you will have to connect the Arduino with a USB-cable to your computer. Next, navigate to the ‘main.cpp’ file (depending on which one you chose earlier on) in the ‘src’ folder.

Once you are in this file, the first thing you need to know is which variables to include in line 11 (Fig.16). We created a second set of variables called ‘variables_DEV’ that give access to a ‘development mode’ in the Robotic Flower. This is made so you can more easily check the functioning of the flower and track any problems if needed, e.g. by faster sending times, keeping the serial monitor open and a LED signalling the state of the flower (see section 5.5.2). To include ‘variables’ or ‘variables_DEV’, you will have to change this in the file by writing the name of the chosen one.

To build the firmware, press the little ‘ ’ in the bottom right, next to upload the built firmware to the Arduino press the ‘ ‘-button (Fig.16). When uploading is successful, the terminal will tell you so and

then you can open the serial monitor with the ‘ ’-button.

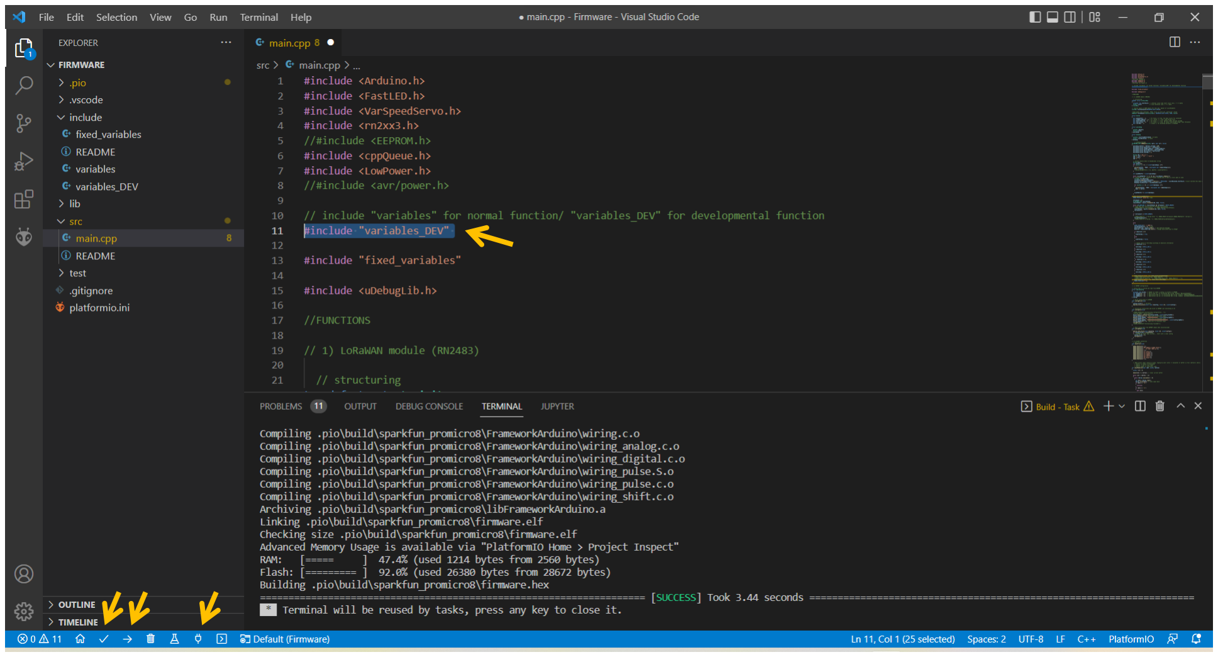
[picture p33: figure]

Figure 16

5.5 INITIALIZING THE FLOWER

The first time a new robotic flower is connected, the parameters that are needed to make connection with an IoT network must be stored in the permanent memory of the microcontroller. To do this, upload the firmware in development mode, i.e. with including the

‘variables_DEV’, and open the serial monitor with the ‘ ’-button in the bottom left (see Fig. 16). After some seconds, a menu will show up (Fig. 17). When you type 1 in the command line and press enter, the serial monitor will show the current parameters (initialized at all 0’s when not entered before). Here you will be able to find the DevEUI you need to complete part ‘4. Setup IoT’, where devices should be added to the application. By typing 2 in the menu, the DevEUI can be altered manually, but this should not be necessary. Typing 3 and 4 respectively in the menu lets you
configure the AppEUI and AppKey (see part ‘3. Setup IoT’).

When all these parameters have been set you can type 0 in the command line to start the functioning of the flower for real. Moreover, when switching on battery power, you will also see the LED light signalling the functioning and the movement of the servo arm (we recommend not attaching the servo arm yet, as the position of the servo needs to be initialized first, see ‘7.1 Preparations’).

5.5.1 SERIAL MONITOR
In development mode, you can follow what is happening on the serial monitor in your computer. With prints coming from the Arduino through the USB-cable, you can see where in the firmware the Arduino is operating.

If you want or don’t want to see the reading of the IR-sensor in the serial monitor during development mode, you can specify this in the top of the ‘variables_DEV’ file in the folder ‘Include’ in VSC. Putting True or False after ‘SHOW_VALUE’ will do the trick. Seeing the values can help you make sure the detection system works as it should be: put something like a pencil inside the feeding hole and you should see a significant drop in the IR-value. In ours, the baseline (no visit) value is approx. 950.

To more easily test the flower with sleep mode, there also is a variable ‘DEV_SLEEP_MODE’ that can be on True or False in the ‘variables_DEV’ file. This is because the regular sleep mode puts the Arduino in a power saving state which automatically breaks of the serial connection, meaning that the serial monitor will stop working.

### 5.5.2 LED SIGNALS

The LED only works when the battery is switched on (just like the servo motor the LED works on 5V, unlike the voltage coming through the Arduino which is 3.3V only).

Led signals during starting up: begins with red, it goes out when looking for serial monitor, red again when attempting to make connection and finally blinking green when connection is established. Following signals will give indications (only when the flower is in Development mode):

- | Blinking green | every second = working mode, battery normal
- | Blinking | red | every half second = working mode, battery warning (can become very dim when
battery almost empty)
- | Continuously | red | = detecting a visit
- | Flashing | bright blue | = end of visit and visit saved
- | Continuously | yellow | = sending data over LoRaWAN
- | Continuously | deep blue = in sleep mode

Figure 17

5.5.3 OPERATIONAL MODE
When putting flower in operational mode by including ‘variables’ in stead of ‘variables_DEV’, the flower will not longer show LED signals after connection is made and the serial monitor will be closed together with the USB communication on the Arduino to save battery power.

Once the program is on the Arduino, it will start running from the moment when the battery is powered on, so opening the serial monitor with the USB-cable etc. is not longer necessary. If no serial connection is detected, the flower automatically proceeds to working.

!! Note that, to upload new variables or put the flower back in development mode, you will need to take away all the power sources to the Arduino (battery and USB) before connecting the USB again and upload the firmware again before the USB communication is blocked when the flower is starting up.

## 6 NECTAR CUP VOLUME

6.1 ADAPT NECTAR VOLUME

The nectar cup volume can be altered by opening the 3D design in Fusion360 and changing the parameters determining the depth and/or shape of the hole in the cup that will hold the nectar (see also ‘2.3 3D-printing & Assembly’).

6.2 DIFFERENT DESIGNS READY AVAILABLE

For the prototype we made a cup with a volume of approximately 15 µL (see also 2.3.3 Nectar cup), but later we also created different designs to offer other discrete nectar volumes. These volumes were determined by measuring with capillary tubes after refilling (see ‘6.3 volume measurement’; Corbet (2003)).

Available on GitHub:

- 22 µL
- 15 µL
- 12 µL
- 8.5 µL
- 6.4 µL
- 4.5 µL

6.3 VOLUME MEASUREMENT

The volumes of the nectar cups were measured using Drummond (Broomall, U.S.A.) microcaps® for microsampling. 10 µL micropipettes were used, which means that for the larger volumes multiple capillaries were used.

The robotic flower nectar reservoir was filled with artificial nectar with a 40% sugar concentration. By manually triggering the IR detection system, the robotic flower refilled the nectar that then was extracted with the capillary tubes. Next, the nectar in each capillary tube was measured with a digital precision vernier caliper. To determine the volume, first a calibration to the used nectar concentration solution was needed. The calibration was done with µL of the solution, which led to an average distance of 18.66 mm, which means that 1 µL equals 3.73 mm.

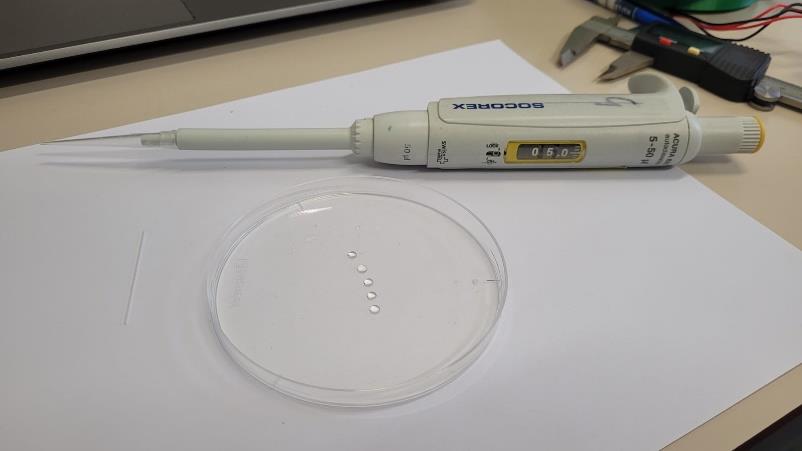
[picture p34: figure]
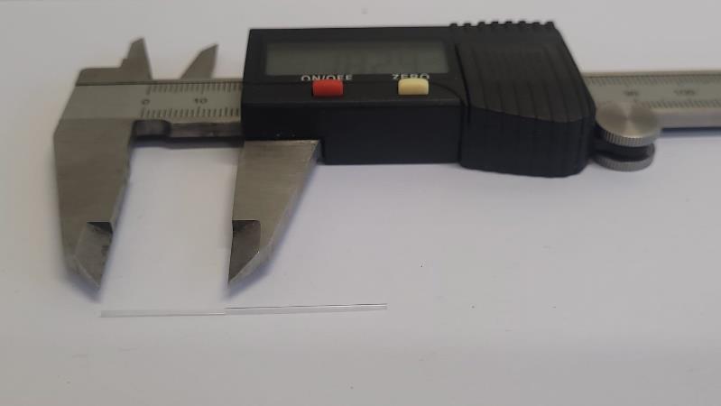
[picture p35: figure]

Each nectar cup was measured 10 times (see measurements) in order to calculate the volume and standard deviation:

# Results

Nectar cup Average volume (µL) | Std dev.
1 | 22.22907064 | 0.39372117
2 | 14.97454175 | 0.49050656
3 | 12.09507986 | 0.505986598
4 | 8.513506271 | 0.323942432
5 | 6.351966985 | 0.14375323
6 | 4.543627398 | 0.260787202

## Callibration (5 µL)

Measurement | Capillary distance (mm)
1 | 18.64
2 | 18.61
3 | 18.68
4 | 18.79
5 | 18.58
6 | 18.6
7 | 18.59
8 | 18.76
9 | 18.67
10 | 18.66

## Mean dist. 5 µL = 18.66 Dist. 1 µL = 3.73

# Measurements

Nectar cup Measurement Capillary distance (mm) | Volume
1 | 1 | 80.93 | 21.68774788
1 | 2 | 83.4 | 22.34966234
1 | 3 | 84.14 | 22.5479687
1 | 4 | 81.04 | 21.71722585
1 | 5 | 85.84 | 23.00353736
1 | 6 | 82.56 | 22.12455783
1 | 7 | 81.89 | 21.94501018
1 | 8 | 83.12 | 22.27462751
1 | 9 | 82.98 | 22.23711009
1 | 10 | 83.6 | 22.40325866
2 | 1 | 59.09 | 15.83503055
2 | 2 | 56.26 | 15.07664273
2 | 3 | 55.89 | 14.97748955
2 | 4 | 56.02 | 15.01232715
2 | 5 | 53.98 | 14.46564476
2 | 6 | 54.89 | 14.70950799
2 | 7 | 55.69 | 14.92389324
2 | 8 | 54.4 | 14.57819702
2 | 9 | 58.12 | 15.57508843
2 | 10 | 54.45 | 14.5915961
3 | 1 | 42.19 | 11.30614214
3 | 2 | 43.6 | 11.68399614
3 | 3 | 44.37 | 11.89034194
3 | 4 | 46.57 | 12.47990138
3 | 5 | 48.94 | 13.11501769
3 | 6 | 46.35 | 12.42094544
3 | 7 | 44.35 | 11.88498231
3 | 8 | 43.82 | 11.74295208
3 | 9 | 44.7 | 11.97877586
3 | 10 | 45.35 | 12.15296388
4 | 1 | 33.03 | 8.851431022
4 | 2 | 29.95 | 8.026047808
4 | 3 | 32.96 | 8.832672312
4 | 4 | 31.86 | 8.537892593
4 | 5 | 31.3 | 8.387822918
4 | 6 | 32.25 | 8.642405403
4 | 7 | 32.91 | 8.819273234
4 | 8 | 29.78 | 7.980490942
4 | 9 | 31.08 | 8.328866974
4 | 10 | 32.57 | 8.728159503
5 | 1 | 22.99 | 6.16089613
5 | 2 | 23.72 | 6.356522671
5 | 3 | 23 | 6.163575946
5 | 4 | 24.33 | 6.519991425
5 | 5 | 23.82 | 6.383320828
5 | 6 | 24.21 | 6.487833637
5 | 7 | 22.96 | 6.152856683
5 | 8 | 23.98 | 6.426197878
5 | 9 | 24.24 | 6.495873084
5 | 10 | 23.78 | 6.372601565
6 | 1 | 15.86 | 4.250187587
6 | 2 | 17.46 | 4.678958088
6 | 3 | 18.13 | 4.858505735
6 | 4 | 16.04 | 4.298424268
6 | 5 | 17.33 | 4.644120485
6 | 6 | 17.18 | 4.60392325
6 | 7 | 17.21 | 4.611962697
6 | 8 | 18.04 | 4.834387394
6 | 9 | 17.18 | 4.60392325
6 | 10 | 15.12 | 4.051881231

## 7 STEPS TO PREPARE A TRIAL

7.1 PREPARATIONS

Now that we have our flowers ready to collect data, we will need to set them up in the correct way to make them work as long as we want.

1. First, we will need to get the batteries charged. A fully charged battery can power a robotic flower for approximately two weeks (see part ‘8. Battery life estimation’). You can charge the batteries using the battery module with the micro USB port, but it can also be convenient to have a separate charger. In this way you can have spare batteries charging while the flowers are working.
2. Then, it can be useful later to have all the flowers labelled on the outside with a sticker (or in another way) with the same device name you put in the application before (part ‘4. Setup IoT’). For example, label them with numbers, so that you easily can see which flower is which during the trial.
3. Make sure all parts are clean and dry. Especially if they have been used before, make sure all leftover artificial nectar is cleaned. Watch out, as 3D printed parts are not suited for the dishwasher! Best is to just use semi-hot water and soap to clean these parts. See in ‘10. Troubleshooting’ the part about cleaning PCB.
4. Probably you will want to offer some kind of reward to the visitors in the robotic flower. You can make any solution you need for your experiment and fill the nectar reservoir. It is best to fill it with at least 40 ml, but you can go up to 80 ml (that is, if you use the same container we did; see also part ‘3.3.5 Nectar reservoir’). But don’t put it inside the flower yet, as the flowers will need to be moved. To prevent any spilling, we place it in the nectar reservoir case (see part ‘3.3.4 Reservoir case’) only as a last step of the flower setup.

7.2 ATTACHING SERVO ARM

Something we didn’t do yet is attaching the servo arm. See Fig. 8 for an example of an attached servo arm. The first step is to attach the steel wire to the nectar cup (see part ‘3.3.3 Nectar cup’) at one side and the spindle on the other side. While doing this, keep in mind the distance between the nectar hole and the servo motor to choose the length of your steel wire (better to take it a little bit too long than too short). When this is done, we can now start to attach it to the servo motor in the right way as to ensure good alignment with the nectar hole.

1. The start is to get the right distance and angle in the steel wire. Attach the servo arm to the servomotor by pushing the spindle on the gear, as if it would be in closed position. Now you can bend the steel wire until the nectar cup fits nicely the notch in the central flower disk. You can check the nectar cup alignment with the feeding hole by looking from above. When this step is done, take the servo arm of again.
2. Next, make sure the servo is in closed position. To do this, the flower needs to be working on battery power. The easiest ways to proceed from here is to put the flower in development mode, or have the refilling rate at e.g. 30 seconds via Node-RED. Now wait until you hear the flower refilling at least once, so that you know that the servo is in closed position.
3. Now you can press the spindle on the gear of the servomotor, it doesn’t matter in which position. Then forcibly turn the gear a (little) bit up and take the arm out again. Then attach the servo arm in the right position (touching the hole). This step ensures a tight fit, as the servo arm will be kind of ‘pressed’ against the nectar hole.
4. Now check again if the position is still correct after a couple of servo movements. If not, carefully adjust the steel wire to correct the nectar cup position.

7.3 EXPERIMENTAL SETUP

1. The first step: choose the right firmware variables for your experiment. See part ‘5.3.1 List of adjustable parameters’ to see all the options. Be critical when setting these, also paying attention if the value e.g. is given in seconds or milliseconds. When ready, upload to the Arduino. If nothing has to change since the last used firmware, you can skip this part.
2. Put flowers together:
- Make sure all cables are connected and connectors are plugged in.
- Put the PCB inside the stem, making sure the holes fit the protrusions on the bottom.
- Next, put the battery on top of the PCB in horizontal position, making sure it stays low
- Insert the reservoir case, making sure it fits the protrusions in the stem and the cables going to the servo are at one side in the cable hole and the cables going to the IR-lights are in the other side. The X-marking on the reservoir case should be at the side where the servo arm will go down in the nectar reservoir! Put the reservoir case low enough so that is rests on the support beams in the stem.
- Now you can put the background plane with central flower disk on top and close the robotic flower with the twist-and-lock system.
- The nectar reservoir with artificial nectar can be added later, when flowers are in position.
3. Start Node-RED and open the flow website in your browser. Now you have the option to double click the flow tab for each flower to enable or disable it, e.g. if you’re only using a subset. Disabled flowers will disappear from your dashboard website, so they don’t distract you when monitoring the flowers in use.
4. Important to keep in mind when using Node-RED on a local computer is that you let it run during experiment. This means the computer itself needs to stay on (not in sleep mode), the terminal/ command prompt has to stay open and internet connection should not be disrupted.
5. Now open the dashboard website and set the parameters as you want them:
- Sleep times, ‘Going to sleep at’ and ‘Waking up at’, are not mandatory to set, but will increase the battery life-time. Take in mind the flower will always be sleeping for at least the period of ‘SLEEP_TIME’ defined in the variables. We often set use sleeping from 22 pm to 6 am, with 6h of deep sleep.
- Setting the Refill gap is mandatory. You can choose between the different options you set before (names can be adapted in the Node-RED flow to match the ones you set in ‘Variables’).

6. Set your robotic flowers in the formation and where you want, for example setting them up in patches (blue vs yellow flowers containing nectar of different composition) in a greenhouse or outside (Fig. 18). Tip: make a scheme of the setup with flower numbers and their different treatments.

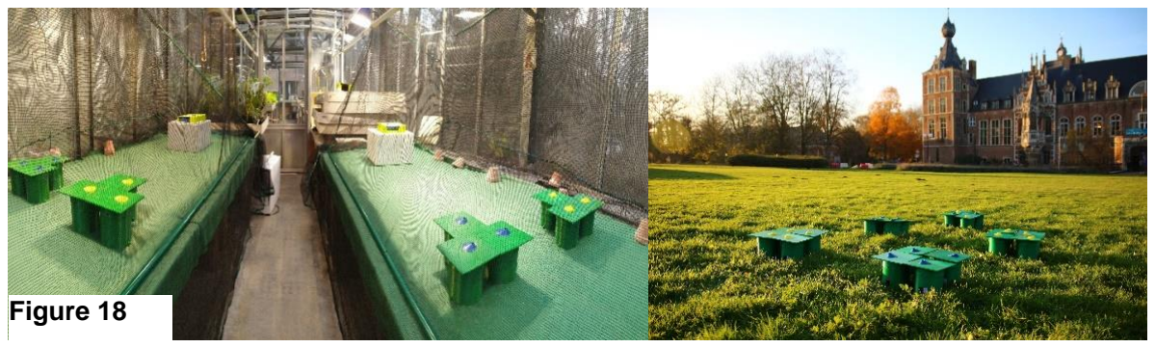
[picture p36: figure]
Figure 18

7. Put the nectar reservoir in the reservoir cage inside the flower and close again. Check if the Xmark on the reservoir cage matches the side of the feeding hole.
8. Switch the flowers on with the switch.
9. Go to dashboard to see if all flowers are connected and working. An easy way to do this is to click battery status and check if all flowers have been sending.
10. Release the study animals and let the data come in!
11. Bonus tip: it can be favourable to start with a learning phase, where the study animals are allowed to discover the robotic flowers in a smaller arena (Fig. 19).

7.4 DURING TRIAL

A daily CSV file will be created in a folder called ‘DataLog’ on the location you have specified in Node-RED ‘file logger flow’ (see part ‘4. Node-RED). Data is added to the bottom of the daily file in real-time. If you change the name or the location of the file of the day while data is still coming in, a new will be started in the ‘DataLog’ folder. Each flower will send its gathered data every 10 minutes. In between sending, these data are saved in RAM, meaning that they are lost when suddenly power is down!

7.4.1 DASHBOARD MONITORING

During the trial you can keep an eye on the functioning of the flowers by looking at the dashboard website (Fig. 13).

Using the ‘Battery’ tab, you can check the last time data has been sent and the battery level of the flowers. To have an idea how long the flowers can keep functioning with the current voltage level, you

Figure 19 can compare with the graph in ‘Fig. 22. Battery voltage over time’. If needed, batteries can be changed during the trial. Be aware though that it might cause some loss of data stored in RAM when the flower loses power. A solution is to do this battery change after going to sleep time. Or you can take the flower out of the arena carefully and connect the battery module to power with micro-USB while changing the battery. This way power continuity is ensured.

In the tab ‘Alarms’ you can check if there are any other problems popping up:
- Queue is full, meaning the flowers RAM is full and no more visits can be stored. This means the flower is getting visits at a higher rate then it can send. Every 10 minutes, data of 16 visits can be send, with a buffer of 100 visits.
- Sending during visit.
- Battery warning, meaning the battery is lower than the specified threshold.
- A possible obstruction of the IR-sensor.

Using a server or running Node-RED in the cloud you can access the dashboard everywhere easily. But what if you are using a local machine for running Node-RED, e.g. on a computer in the lab as we did, but you are at home and want to check out the dashboard? That is possible by installing Node-RED for example on your personal laptop, but here you only put the flower flow (not ‘file logger flow’) and make sure you delete the uplink nodes, so that the flowers only get instructions from the lab computer.

## 8 BATTERY LIFE ESTIMATION

8.1 THEORY

A rechargeable 18650 Li-Ion 3.7 V button-top battery with 3400 mAh (VABO NV, Heusden-Zolder) was used. The number 18650 is based on the size of the battery, which is 18 mm diameter and 65 mm in length.

The batteries have a built-in protection circuit that protects the batteries from overcharging and overdischarging; both could indeed damage the cell and possibly even lead to a safety hazard (fire and/or explosion). Li-Ion cells should be handled with care.

The 3.7 V gives the nominal or average voltage. A fully charged battery will be maximum 4.2 V and in use the voltage will drop until the minimum is reached (Fig. 1; Chen & Rincon-Mora, 2006). Charge time is approximately 5.5 hours according to the manufacturer data sheet.

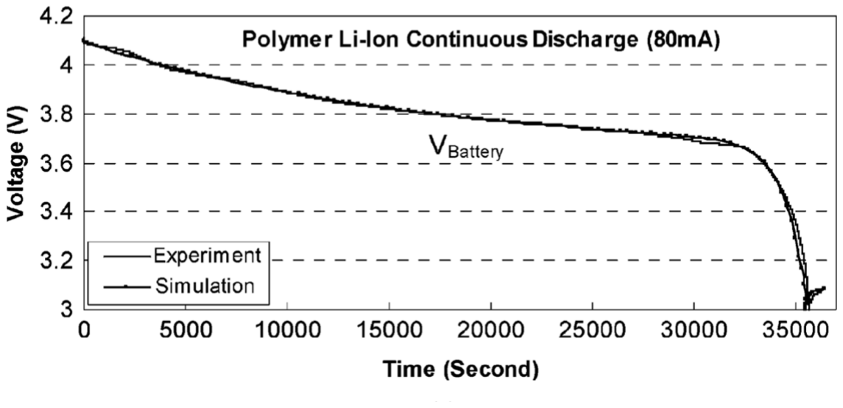
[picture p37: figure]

The 3.7 V Li-Ion batteries that were used here have 3400 mAh (milliampere hour). This value represents the total amount of energy that can be stored in the battery, which combined with the mean energy consumption can give an indication of how long the battery will be able to power the robotic flower.

First, we need to take the conversion of 3.7 V to 5 V in the battery module into account. As the wattage (W = V × I, with V in volts and I in ampere) before and after conversion stays the same, the formula I2 =

V1
V2

⁄ × I1 can be used to determine the new value for mAh. In this case, that gives 2516 mAh, but

there is a loss of energy during the conversion that must be considered. By taking a (wide) margin of 10% loss, the value used for further calculations of battery life is 2264 mAh.

Next, the energy consumption of the robotic flower needs to be known. For this, we performed a 24-hour measurement, containing the work state and the sleep state, to find the mean value for energy consumption of the robotic flower. This was done using JoulescopeTM, a precision energy analyser that can be connected to a computer and, among others, show changes over time like an oscilloscope (Fig. 2). JoulescopeTM was also used during software development to reduce energy consumption. Using parameters 10 pm and 6 am for going to sleep and waking up time respectively with 7 hours of deep sleep and refilling rate as well as sending rate at 10 minutes, the mean value for basal energy consumption (without visitors) over 24 hours was 4.1 mA. This value combined with the battery capacity yields a predicted battery lifetime of 19.56 days according to the Oregon Embedded online battery life calculator¹
(which reduces the lifetime with 15% automatically to account for self-discharge of the battery).

1 https://oregonembedded.com/batterycalc.htm

Figure 20: A typical voltage response curve, showing the maximum voltage around 4.2, the minimum at 3 and the nominal voltage around 3.7 for lithium-ion batteries (Chen & Rincon-Mora, 2006).

This value is an estimation, as several factors might influence the battery life, one of them being the ambient temperature in which the robotic flower is used. Li-Ion batteries usually have an optimal operating temperature between 15°C and 35°C, higher or lower temperatures may affect the battery performance negatively (Ma et al., 2018). For example, when using the robotic flowers in a glasshouse, it is good to know that high temperatures could lead to a reduced lifetime of the batteries.

The mean energy consumption during the work state was around 6.3 mA without floral visitation (basal energy consumption). This value went up to 6.8 mA when a visit of variable length (but longer than the visit threshold of three seconds) was simulated every minute, which is logical as the servomotor will have to work more frequently and the LoRaWAN module will have to send larger data packages each time.

8.2 IN PRACTICE

To test the actual basal (i.e., without pollinators visiting) battery lifetime, we set-up a flower with a fully charged battery (± 4.1V) in an office with a relatively constant temperature around 20 °C. The sleep time was set between 10pm and 6am. For each day, the voltage level was measured 12 times until the flower stopped (± 2.5V). These data are represented in Fig.3, showing the voltage over time. The result was a lifetime of 15 days, but to avoid loss of data because of empty batteries we recommend a 14-day limit. The graph can be used to predict the remaining lifetime of the battery for a given voltage level.

Figure 21: Energy consumption of the robotic flower during working mode and sleep mode with A) the spike of the LoRaWAN module sending data, B) the LoRaWAN module receiving a message after sending, C) the servomotor moving to the open position, D) the servomotor moving to the close position, E) and F) showing two energy consumption spikes during sleep mode. Made with JoulescopeTM.

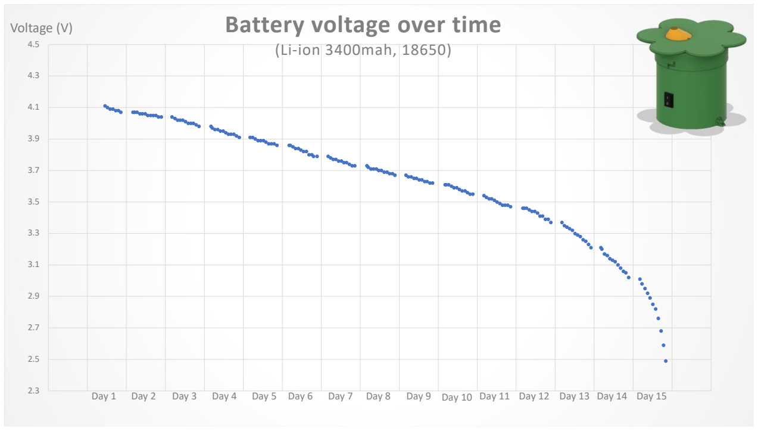
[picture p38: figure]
Battery voltage over time; (Li-ion; 3400mah, 18650); Voltage (V)

## 9 COMBINING WITH RFID SYSTEM FROM MICROSENSYS

# GMBH

We used the Robotic flower in combination woth RFID readers from Microsensys GmbH (https://www.microsensys.de/en/solutions/small-animals-identification/). To do so, we designed a new central flower disk so that RFID readers ‘iID®Reader Block AEB-04.1D (EU)’ could be fit in (Fig. 23). See also part 2.3.2 Background plane and central flower disk (Fig. 7.1, C). The RFID radio waves will make the flowers deaf, meaning they cannot receive instructions anymore, so we created a new firmware version for this combination (see part ‘5.2 Download firmware’). When the flower is put to sleep, it will keep sending data but not expecting an answer. Note that you will have to put the flowers to sleep from the dashboard website before switching on the RFID readers.

Day 1 | Day 2 | Day 3 | Day 4 | Day 5 Day 6 | Day 7 Day 8 | Day 9 Day 10 Day 11 Day 12 Day 13 Day 14 Day 15

Figure 22: Evolution of the robotic flower battery voltage over time.

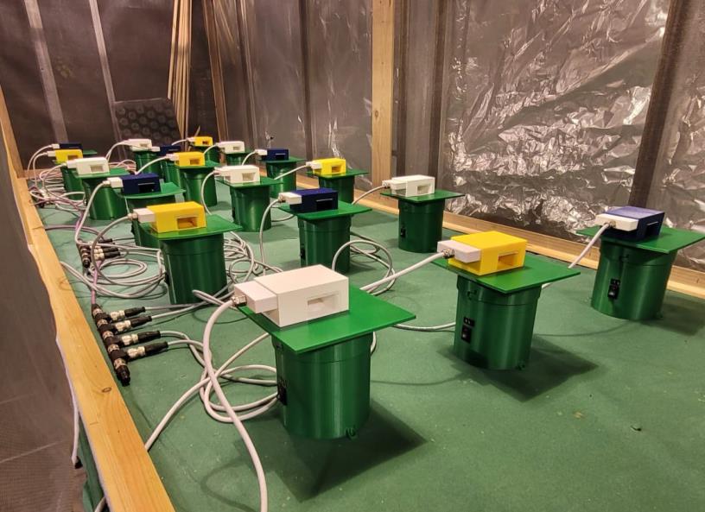
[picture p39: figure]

Figure 23: Flight cage setup with 18robotic flowers combined with RFID readers in a latin-square design

## 10 TROUBLESHOOTING

To check the well-functioning of the robotic flowers, we recommend you to play around with them in the development mode. Here you can follow everything that is happening in the serial monitor. Before use, check if the servo motor and IR detection system is working. If you find a problem, try to deduce what might be the cause by ruling things out step by step. Here we list some things that might happen to your flowers with some hints that might help you solve the problem. If problems persist, feel free to contact us for help!
1. You don’t see the flowers in Node-RED dashboard

➔ Make sure the flowers you want to use are enabled in the Node-RED flow overview.

2. You get a spill on the PCB and need to clean it

➔ Spills on the PCB can lead to small problems, e.g. misreading of battery level, but also to serious malfunctioning. You can clean this, but always use demineralized water to avoid crystals after drying. We had this problem and fixed it with emerging the PCB in a supersonic bath of demineralized water at 50°C for 5 minutes (without antenna) and gently brushing it with a toothbrush. It is very important to let it dry thoroughly before using it again, we used a hot air oven at 50°C for this purpose.

3. A flower did not wake up from sleep mode

➔ Make sure you put the correct sleeping times in Node-RED. By switching the flower off and on again it should reset and start working again. If not, try changing the battery. If the problem exists in all the flowers, check the firmware for any mistakes, e.g. in the variable ‘SLEEP_TIME’.

4. The flower is working, but is seems to be stuck in trying to make connection

➔ Check if Node-RED is running and if all parameters are set correctly in the IoT service you use (e.g. The things Network) and correspond to the parameters set in the flower. Does the flower show the LoRa module version and DevEUI when typing 1 in the start menu in Development mode (see part ‘5.5 Initializing the flower’)? If not, the problem might be due to bad connection of the LoRa module on the PCB. Check if soldering was done correctly and/or if any connections have been made where there should not be. Cleaning the PCB might also help (see Troubleshooting 3).

5. The flower has suddenly stopped sending data

➔ Check if the battery is still charged. If that is not the problem, it might be the battery module that is failing. Switching the flower off and on again can reset the flower. If this does not help, check for any hardware problems: is there a cable not connected anymore? Is there a big spill on electronics?

6. The flower does not detect any visits

➔ Put the flower in development mode and check the IR values the flower is receiving. You should see a drop in this value when you manually block the sensor. If not, it might be the sensor or emitter is broken or not connected correctly.

7. The flower does not start working and the battery module does not show any LED light when switched on

➔ First check if the battery is charged and inserted correctly (+ and -). If that is not the problem, you can try to reset the battery module by connecting it shortly with the micro-USB port to a power source. If this is still not working, try with another battery module.

## 11 REFERENCES

Balfour, N. J., Garbuzov, M., & Ratnieks, F. L. W. (2013). Longer tongues and swifter handling: why do more bumble bees (Bombus spp.) than honey bees (Apis mellifera) forage on lavender (Lavandula spp.)? ECOLOGICAL ENTOMOLOGY, 38(4), 323–329. https://doi.org/10.1111/een.12019

Branquart, E., & Hemptinne, J. L. (2000). Selectivity in the exploitation of floral resources by hoverflies
(Diptera : | Syrphinae). | ECOGRAPHY, | 23(6), | 732–742. | https://doi.org/10.1034/j.1600-
0587.2000.230610.x

Chen, M., & Rincon-Mora, G. A. (2006). Accurate electrical battery model capable of predicting, runtime and I-V performance. IEEE TRANSACTIONS ON ENERGY CONVERSION, 21(2), 504–511. https://doi.org/10.1109/TEC.2006.874229

Corbet, S. A. (2000). Butterfly nectaring flowers: butterfly morphology and flower form. ENTOMOLOGIA
EXPERIMENTALIS | ET | APPLICATA, | 96(3), | 289–298. | https://doi.org/10.1046/j.1570-
7458.2000.00708.x

Kuusela, E., & Lämsä, J. (2016). A low-cost, computer-controlled robotic flower system for behavioral experiments. ECOLOGY AND EVOLUTION, 6(8), 2594–2600. https://doi.org/10.1002/ece3.2062

Ma, S., Jiang, M., Tao, P., Song, C., Wu, J., Wang, J., … Shang, W. (2018). Temperature effect and thermal impact in lithium-ion batteries: A review. Progress in Natural Science: Materials International, 28(6), 653–666. https://doi.org/https://doi.org/10.1016/j.pnsc.2018.11.002

Pozo, M. I., van Kemenade, G., van Oystaeyen, A., Aledon-Catala, T., Benavente, A., den Ende, W., … Jacquemyn, H. (2020). The impact of yeast presence in nectar on bumble bee behavior and fitness. ECOLOGICAL MONOGRAPHS, 90(1). https://doi.org/10.1002/ecm.1393

## 12 APPENDIX

12.1 PARTS LIST

Part | Specifications | Article number | #/flower | Company | URL
Microcontroller Pro Micro | ATMEGA32U4 3.3V/8MHZ | DEV-12587 | 1 | DigiKey | https://www.digikey.be/product-detail/en/sparkfun-electronics/DEV-12587/1568-1061-ND/5140826
Micro Servo | SERVOMOTOR RC 4.8V | SER0006 | 1 | DigiKey | https://www.digikey.be/product-detail/en/dfrobot/SER0006/1738-1385-ND/7597224
LED (per 5) | ADDRESS LED DISCR SERIAL RGB 5PC | COM-12986 | 0.2 | DigiKey | https://www.digikey.be/product-detail/en/sparkfun-electronics/COM-12986/1568-1213-ND/5673799
ON/OFF Switch | SWITCH ROCKER SPST 10A 125V | RA1113112R | 1 | DigiKey | https://www.digikey.be/product-detail/en/e-switch/RA1113112R/EG5619-ND/3778055
IR emitter | EMITTER IR 940NM 50MA RADIAL | IR908-7C-F | 1 | DigiKey | https://www.digikey.be/product-detail/en/everlight-electronics-co-ltd/IR908-7C-F/1080-1089-ND/2675580
IR receiver | SENSOR PHOTODIODE 940NM RADIAL | BPV22NF | 1 | DigiKey | https://www.digikey.be/nl/products/detail/vishay-semiconductor-opto-division/BPV22NF/1681141
Power Switch | IC PWR SWITCH N-CHANNEL 1:1 8DIP | TPS2024P | 1 | DigiKey | https://www.digikey.be/product-detail/en/texas-instruments/TPS2024P/296-12234-5-ND/413526
Level Converter | IC BUF NON-INVERT 5.5V 14DIP | SN74HCT125N | 1 | DigiKey | https://www.digikey.be/product-detail/en/texas-instruments/SN74HCT125N/296-8386-5-ND/376860
Diode | DIODE SCHOTTKY 30V 1A DO41 | 1N5818 | 1 | DigiKey | https://www.digikey.be/product-detail/en/stmicroelectronics/1N5818/497-4548-1-ND/770973
Res 200 | RES 200 OHM 1/2W 1% AXIAL | SFR16S0002000FR5
| | 00 | 2 | DigiKey | https://www.digikey.be/product-detail/en/vishay-beyschlag-draloric-bc-
| | | | | components/SFR16S0002000FR500/PPC200XCT-ND/594751 (https://www.digikey.be/product-detail/en/vishay-beyschlag-draloric-bc-components/SFR16S0002000FR500/PPC200XCT-ND/594751)
| | SFR16S0002001FR5 | | | https://www.digikey.be/product-detail/en/vishay-beyschlag-draloric-bc-
Res 2k | RES 2K OHM 1/2W 1% AXIAL | 00 | 2 | DigiKey | components/SFR16S0002001FR500/PPC2.00KXCT-ND/594777 (https://www.digikey.be/product-detail/en/vishay-beyschlag-draloric-bc-components/SFR16S0002001FR500/PPC2.00KXCT-ND/594777)
Res 10 k | RES 10K OHM 1/2W 1% AXIAL

SFR16S0001002FR5
00 | 3 | DigiKey

https://www.digikey.be/product-detail/en/vishay-beyschlag-draloric-bccomponents/SFR16S0001002FR500/PPC10.0KXCT-ND/594695 (https://www.digikey.be/product-detail/en/vishay-beyschlag-draloric-bc-components/SFR16S0001002FR500/PPC10.0KXCT-ND/594695)
| | MBA02040C1003FRP | | | https://www.digikey.be/product-detail/en/vishay-beyschlag-draloric-bc-
Res 100k | RES 100K OHM 0.4W 1% AXIAL | 00 | 2 | DigiKey | components/MBA02040C1003FRP00/BC100KXCT-ND/336963 (https://www.digikey.be/product-detail/en/vishay-beyschlag-draloric-bc-components/MBA02040C1003FRP00/BC100KXCT-ND/336963)
Capacitor 100nF | CAP CER 0.1UF 50V X7R RADIAL | C322C104K5R5TA73
| | 01 | 8 | DigiKey | https://www.digikey.be/product-detail/en/kemet/C322C104K5R5TA7301/399-9877-1-ND/3726183
Capacitor 33uF | CAP ALUM POLY 33UF 20% 20V T/H | RNS1D330MDS1 | 2 | DigiKey | https://www.digikey.be/product-detail/en/nichicon/RNS1D330MDS1/493-14237-ND/4991537
Antenna | RF ANT 868MHZ WHIP STR SMA MALE | ANT-868-CW-RH-
| | SMA | 1 | DigiKey | https://www.digikey.be/product-detail/en/linx-technologies-inc/ANT-868-CW-RH-SMA/ANT-868-CW-RH-
| | | | | SMA-ND/1962848 (https://www.digikey.be/product-detail/en/linx-technologies-inc/ANT-868-CW-RH-SMA/ANT-868-CW-RH-SMA-ND/1962848)
Antenna connector | CONN SMA RCPT STR 50 OHM PCB | 733910060 | 1 | DigiKey | https://www.digikey.be/product-detail/en/molex/0733910060/WM5543-ND/1465165
Cable conn. on/off | JST-XH
male | CONN HEADER VERT 2POS 2.5MM | B2B-XH-A-M(LF)(SN) | 1 | DigiKey | https://www.digikey.be/product-detail/en/jst-sales-america-inc/B2B-XH-A-M-LF-SN/455-2879-
| | | | | ND/3926507 (https://www.digikey.be/product-detail/en/jst-sales-america-inc/B2B-XH-A-M-LF-SN/455-2879-ND/3926507)
power connector 3p male (pcb) | TERM BLOCK HDR 3POS VERT 3.5MM | 395016003 | 1 | DigiKey | https://www.digikey.be/product-detail/en/molex/0395016003/WM25698-ND/2735251
power connector 3p female | TERM BLOCK PLUG 3POS 3.5MM | 395038003 | 1 | DigiKey | https://www.digikey.be/product-detail/en/molex/0395038003/WM25709-ND/4480336
in/output connector 7p male | TERM BLOCK HDR 7POS VERT 3.5MM | 395016007 | 1 | DigiKey | https://www.digikey.be/product-detail/en/molex/0395016007/WM25702-ND/2735255

in/output connector 7p female | TERM BLOCK PLUG 7POS 3.5MM | 395037007 | 1 | DigiKey | https://www.digikey.be/product-detail/en/molex/0395037007/WM25519-ND/4480323
| | | | | https://www.digikey.be/product-detail/en/sullins-connector-solutions/PPTC121LFBN-RC/S6100-
conn headers female 12p | CONN HDR 12POS 0.1 TIN PCB | PPTC121LFBN-RC | 2 | DigiKey | ND/807231 (https://www.digikey.be/product-detail/en/sullins-connector-solutions/PPTC121LFBN-RC/S6100-ND/807231)
plug-in IC sockets 4x2p | CONN IC DIP SOCKET 8POS TIN | A 08-LC-TT | 2 | DigiKey | https://www.digikey.be/product-detail/en/assmann-wsw-components/A-08-LC-TT/AE9986-ND/821740
plug-in IC sockets 7x2p | CONN IC DIP SOCKET 14POS TIN | A 14-LC-TT | 1 | DigiKey | https://www.digikey.be/product-detail/en/assmann-wsw-components/A-14-LC-TT/AE9989-ND/821743
EEPROM | 512 Kbit, 64K x 8bit, Serial I2C (2-Wire), 400 kHz,
| DIP, 8 Pins | 24LC512-I/P | 1 | Farnell | https://be.farnell.com/microchip/24lc512-i-p/serial-eeprom-512kbit-400khz-
| | | | | dip/dp/9758020?CMP=GRHB-OCTOPART (https://be.farnell.com/microchip/24lc512-i-p/serial-eeprom-512kbit-400khz-dip/dp/9758020?CMP=GRHB-OCTOPART)
| | | | | https://be.farnell.com/microchip/rn2483a-i-rm104/transceiver-module-300kbps-
LoRaWAN module | RN2483A-I/RM104 or RN2483A-I/RM105 | RN2483A-I/RM104 | 1 | Farnell | 870mhz/dp/2920841?st=rn2483 (https://be.farnell.com/microchip/rn2483a-i-rm104/transceiver-module-300kbps-870mhz/dp/2920841?st=rn2483)
Coating spray | PLASTIK 70 conformal coating | 2646050 | / | Farnell | https://be.farnell.com/kontakt-chemie/plastik-70/conformal-coating-aerosol-200ml/dp/2646050
Battery | Li-ion 3500mah, 18650, flat top | 12429 | 1 | VaBo | http://www.vabo.be/ned/ned_main.htm
Silicone | Transparant sanitary Kit Handson 310 ml | 604449 | / | Gamma | https://www.gamma.nl/assortiment/handson-sanitairkit-transparant-310-ml/p/B604449
Tie wraps (100 pcs.) | 200x2,5 mm 100p, Handson | 110695 | / | Gamma | https://www.gamma.nl/assortiment/handson-bindband-zwart-2-5-x100-mm-100-stuks/p/B110695
Solder tin | 0.7 mm tin/copper 50 gram, Griffon | 607125 | / | Gamma | https://www.gamma.nl/assortiment/griffon-printsoldeer-0-7-mm-tin-koper-50-gram/p/B607125
PCB | Printed Circuit Board | / | 1 | JLCPCB | https://jlcpcb.com/
3D Pint | PLA print using | / | 1 | FabLab | https://fablab-leuven.be/?lang=en
| | | | KIWI
wire | Silicon flexible wire, 7.5m 26AWG | KW-2371 | / | electronics | https://www.kiwi-electronics.nl/kw-2371?search=Siliconen%20Draad%20Soepel&description=true
12 pin header | 40 pin header strip | KW-2424 | 0.66

KIWI
electronics | https://www.kiwi-electronics.nl/40-pin-header-strip?search=header%20pins&description=true
| | | | KIWI
quick conn. on/off tab (10 pcs) | Tabs till 4.8mm, 2.54mm JST-XH - male | KW-2310 | 0.1 | electronics | https://www.kiwi-electronics.nl/kw-2310

Plastic containers

IN: 56x36x50 mm, OUT: 60x40x52(LxBxH), with
lid | 31185 | 0.1 | Bodemschat | https://www.bodemschat.nl/en/plastic-box-60-x-40-x-52-mm.html
| 5V Micro USB 18650 Lithium Battery
Battery Module | Charger,UPS module Step up | / | 1 | AliExpress | https://nl.aliexpress.com/store/4706110?spm=a2g0o.detail.1000007.1.165664d57AGZiY

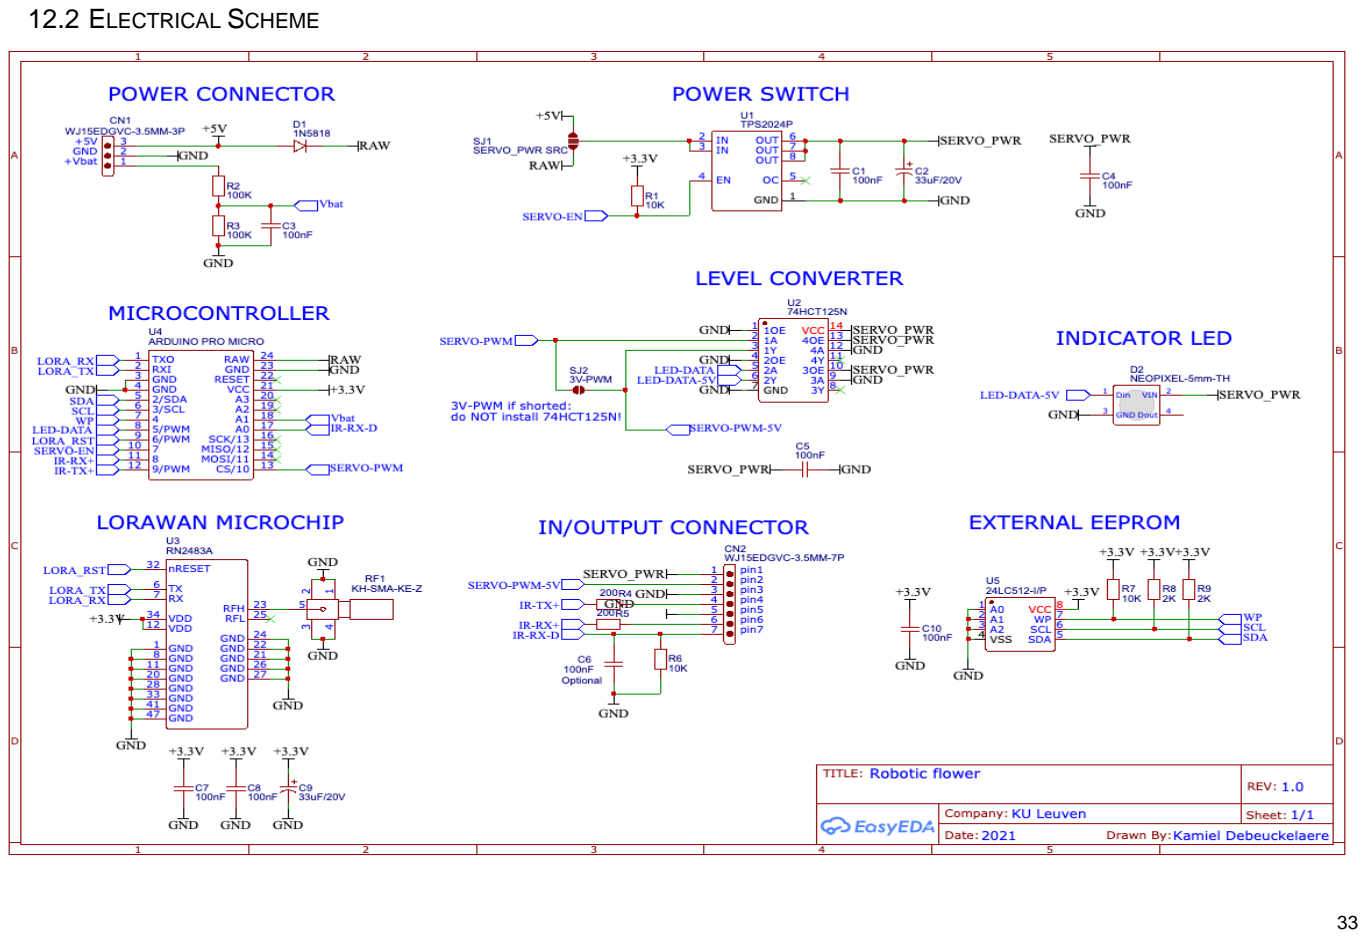
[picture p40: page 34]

12.2 ELECTRICAL SCHEME

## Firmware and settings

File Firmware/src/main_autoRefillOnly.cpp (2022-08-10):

#include <Arduino.h>
#include <FastLED.h>
#include <VarSpeedServo.h>
#include <rn2xx3.h>
//#include <EEPROM.h>
#include <cppQueue.h>
#include <LowPower.h>
//#include <avr/power.h>

// include "variables" for normal function/ "variables_DEV" for developmental function
#include "variables"

#include "fixed_variables"

#include <uDebugLib.h>

//FUNCTIONS

// 1) LoRaWAN module (RN2483)

  // structuring
typedef struct strVisitRec
{
  unsigned long startVisit; // internal clock time start visit (sec.) --> 4 bytes
  uint8_t visit;            // visit duration (sec.) --> 1 byte
} visitRec;

// reserve space in SRAM memory for this max. amount of visitElements
visitRec visitContainer[RESERVED_VISIT_SPACE]; 

//make queue from container, FIFO: first in first out, overwrite = false
cppQueue visitQueue(sizeof(visitRec), RESERVED_VISIT_SPACE, FIFO, false);

struct Alarms
{
  bool queueIsFull : 1;     // 0= false, 1= true, too many visits for container
  bool sendDuringVisit : 1; // 0 = false, 1 = true, send during visit
  bool batteryWarning : 1;  // 0= false, 1 = true, battery under warning voltage
  bool obstruction : 1;     // 0= false, 1 = true, IR sensor obstructed longer than threshold
  bool startBit : 1;        // always 1, for decoding purposes in NodeRed
};

struct uplinkmsg
{
  uint16_t battery;
  Alarms alarms;
} uplinkmsg;

struct datamsg
{
  uint16_t startTimeBeforeSend; //2 bytes
  uint8_t visitDuration; //1 byte
} datamsg;

    // sending message
TX_RETURN_TYPE SENDdata(uint8_t port, bool cnf = false)
{
  uplinkmsg.battery = Battery_voltage * 100;
  uplinkmsg.alarms.queueIsFull = queueIsFull;
  uplinkmsg.alarms.sendDuringVisit = sendDuringVisit;
  uplinkmsg.alarms.batteryWarning = batteryWarning;
  uplinkmsg.alarms.obstruction = obstruction;
  uplinkmsg.alarms.startBit = 1;

  String cmd = "mac tx ";
  cmd += (cnf) ? "cnf " : "uncnf ";
  cmd += port;
  cmd += " ";

  // Convert binary data to hexadecimal string
  String data;
  char buffer[3];
  for (uint8_t i = 0; i < sizeof(uplinkmsg); i++)
  {
    sprintf(buffer, "%02X", ((unsigned char *)&uplinkmsg)[i]);
    data += buffer;
    //memcpy(&msgBuffer[i * 2], &buffer, sizeof(buffer));
  }

  int sizeOfBuffer = sizeof(uplinkmsg);

  while ((sizeOfBuffer + 5 <= 53) && (!visitQueue.isEmpty()))
  { //checking if max. sending 53 bytes reached and if there is still data to send
    visitRec visitRec2send;
    visitQueue.pop(&visitRec2send);
    datamsg.startTimeBeforeSend = (millis() / PRECISION) - visitRec2send.startVisit; //visit started this many seconds before sending
    datamsg.visitDuration = visitRec2send.visit;

    for (uint8_t i = 0; i < sizeof(datamsg); i++)
    {
      sprintf(buffer, "%02X", ((unsigned char *)&datamsg)[i]);
      data += buffer;
    }

    sizeOfBuffer += sizeof(datamsg);
  }

  DEBUG_PRINT(sizeOfBuffer);
  DEBUG_PRINT(F(" bytes")); //dev.

  retryCount = 0;
  TX_RETURN_TYPE resultOfSend;
  resultOfSend = myLora.txCommand(cmd, data, false);

  while ((TX_WITH_RX != resultOfSend) && retryCount < RETRY_AMOUNT)
  { //send data and receive downlink message from backend
    //DEBUG_PRINT(F("resultOfSend: ")); DEBUG_PRINTLN(resultOfSend);
    resultOfSend = myLora.txCommand(cmd, data, false);
    retryCount++;
  }

  if (retryCount == RETRY_AMOUNT)
  {
    DEBUG_PRINT(F(" -> Failed after ")); DEBUG_PRINT(retryCount);DEBUG_PRINTLN(F(" retries"));
    failedToSendCount++;
    DEBUG_PRINT(F("# Failed: ")); DEBUG_PRINTLN(failedToSendCount);
  }

  else
  {
    DEBUG_PRINTLN(F(" -> SEND"));
    failedToSendCount = 0; //reset
    downlinkString = myLora.getRx(); // get downlink message
    downlink = downlinkString.toInt(); //change downlinkString to integer

    if (downlink == 0)
    {
      timeToSleep = true;
    }
    else
    {
      timeToSleep = false;
    }

    // change value of refillGap according to donwlink information
    if (downlink == 1)
    {
      refillGap = REFILL_GAP_1;
    }
    if (downlink == 2)
    {
      refillGap = REFILL_GAP_2;
    }
    if (downlink == 3)
    {
      refillGap = REFILL_GAP_3;
    }
     if (downlink == 4)
    {
      refillGap = REFILL_GAP_4;
    }
    if (downlink == 5)
    {
      refillGap = REFILL_GAP_5;
    }
    if (downlink == 6)
    {
      refillGap = REFILL_GAP_6;
    }

    DEBUG_PRINT(F("Sleep: ")); DEBUG_PRINTLN(timeToSleep);
    //DEBUG_PRINT(downlinkString); DEBUG_PRINT(F(" - "));
    //DEBUG_PRINT(F("downlink: ")); DEBUG_PRINT(downlink); DEBUG_PRINT(F(" - ")); 
    DEBUG_PRINT(F("Refill: ")); DEBUG_PRINT(refillGap);DEBUG_PRINTLN(F(" sec."));
    DEBUG_PRINTLN(F(""));
  }
}

// 2) EEPROM configuration

// Config that is stored and read from EEPROM
struct eepromConfig
{
  unsigned long writes; // Number of times a config is written to EEPROM
  char DevEUI[16 + 1];  // Device EUI as a \0 terminated HEX string. Example "0011223344556677"
  char AppEUI[16 + 1];  // Application EUI as a \0 terminated HEX string. Example "70B3D57ED00001A6"
  char AppKey[32 + 1];  // Application key as a \0 terminated HEX string. Example "A23C96EE13804963F8C2BD6285448198"
} config;

  // Write config data to EEPROM
void configWrite(void)
{
  config.writes++; // Increase
  eeprom_write_block((const void *)&config, (void *)0, sizeof(config));
}

  // Initialise config data and write to EEPROM (set everything to 0)
void configInit(void)
{
  //DEBUG_PRINTLN(F("Initializing configuration..."));
  //String hwEUI = myLora.hweui();
  myLora.hweui().toCharArray(config.DevEUI, sizeof(config.DevEUI));
  config.DevEUI[16] = 0; //add zero to terminate input
  memcpy(config.AppEUI, "0000000000000000", sizeof(config.AppEUI));
  config.AppEUI[16] = 0; //add zero to terminate input
  memcpy(config.AppKey, "00000000000000000000000000000000", sizeof(config.AppKey));
  config.AppKey[32] = 0; //add zero to terminate input
  configWrite();
  //DEBUG_PRINTLN(F("Initializing finished"));
}

  // Read config data from EEPROM (empty when uninitialised)
void configRead(void)
{
  eeprom_read_block((void *)&config, (void *)0, sizeof(config));
  if (config.writes == 0xFFFFFFFF)
  { // EEPROM has never been written... start with a clear config
    config.writes = 0;
    configInit();
  }
}

// 3) DingNet connection
  // Menu print
void menuPrint(void)
{
  DEBUG_PRINTLN(F(""));
  DEBUG_PRINTLN(F(" ONE ROBOTIC FLOWER"));
  DEBUG_PRINTLN(F(" TO STUDY THEM ALL"));
  DEBUG_PRINTLN(F(""));
  DEBUG_PRINTLN(F(" [1] Info"));
  DEBUG_PRINTLN(F(" [2] Set DevEUI"));
  DEBUG_PRINTLN(F(" [3] Set AppEUI"));
  DEBUG_PRINTLN(F(" [4] Set AppKey"));
  DEBUG_PRINTLN(F(" [0] Start"));
  DEBUG_PRINTLN(F(" [R] Reset"));
  DEBUG_PRINTLN(F(""));
}

  // Read serial input (choice of menu, typing by user) until \r encounter or buffer is full (buflen-1 chars).
    // buffer is always 0 terminated!
    // Remove \r and \n from input
    // Return number of characters read
int inputReadline(char *buf, uint8_t buflen)
{
  uint8_t cnt = 0;

  memset(buf, 0, buflen); // Clear current buffer

  while (cnt < (buflen - 1))
  {
    while (Serial.available() > 0)
    {
      int data = Serial.read();
      Serial.write(data); // echo input back
      if (data == '\n')
      {
        continue;
      }
      if (data == '\r')
      {
        goto done;
      }
      buf[cnt] = data;
      cnt++;
    }
    delay(1); // Wait a little before checking serial again
  }
done:
  DEBUG_PRINTLN(F("")); // Print a newline
  return cnt;
}

  // Check if the first 'len' characters of 'buf' are a hexadecimal string
    // Also modify buf and uppercase all characters
    // returns true if all checks ok, false otherwise
bool verifyHexstring(char *buf, uint8_t len)
{
  for (uint8_t i = 0; i < len; i++)
  {
    if (isHexadecimalDigit(buf[i])) // test if hexadecimal
    {
      buf[i] = toupper(buf[i]); // to uppercase
    }
    else
    {
      // Invalid input
      return false;
    }
  }
  return true;
}
#define serialBuflen 64 // Length of serial inputbuffer

// Handle user input in Serial Monitor
void serialHandler(void)
{
  char buf[serialBuflen];
  int len;
  char cmd;

  menuPrint();

  while (1)
  {
    DEBUG_PRINT(F("Command > "));
    len = inputReadline(buf, serialBuflen);

    if (len != 1)
    {
      DEBUG_PRINTLN(F("Invalid input"));
      continue;
    }

    cmd = buf[0]; // store 1st character in different variable (cmd) since we reuse buf
    switch (cmd)
    {
    case '1':
      DEBUG_PRINT(F("Config writes: "));
      DEBUG_PRINTLN(config.writes);
      DEBUG_PRINT(F("Radio version: "));
      DEBUG_PRINTLN(myLora.sysver());
      DEBUG_PRINT(F("HwEUI: "));
      DEBUG_PRINTLN(myLora.hweui());
      DEBUG_PRINT(F("DevEUI: "));
      DEBUG_PRINTLN(config.DevEUI);
      DEBUG_PRINT(F("AppEUI: "));
      DEBUG_PRINTLN(config.AppEUI);
      DEBUG_PRINT(F("AppKey: "));
      DEBUG_PRINTLN(config.AppKey);
      break;
    case '2':
      DEBUG_PRINT(F("Enter DevEUI: "));
      len = inputReadline(buf, serialBuflen);
      if (verifyHexstring(buf, 16))
      {
        memcpy(config.DevEUI, buf, sizeof(config.DevEUI));
        configWrite();
        DEBUG_PRINTLN(F("DevEUI saved"));
      }
      else
      {
        DEBUG_PRINTLN(F("ERROR: Invalid key"));
      }
      break;
    case '3':
      DEBUG_PRINT(F("Enter AppEUI: "));
      len = inputReadline(buf, serialBuflen);
      if (verifyHexstring(buf, 16))
      {
        memcpy(config.AppEUI, buf, sizeof(config.AppEUI));
        configWrite();
        DEBUG_PRINTLN(F("AppEUI saved"));
      }
      else
      {
        DEBUG_PRINTLN(F("ERROR: Invalid key"));
      }
      break;
    case '4':
      DEBUG_PRINT(F("Enter AppKey: "));
      len = inputReadline(buf, serialBuflen);
      if (verifyHexstring(buf, 32))
      {
        memcpy(config.AppKey, buf, sizeof(config.AppKey));
        configWrite();
        DEBUG_PRINTLN(F("AppKey saved"));
      }
      else
      {
        DEBUG_PRINTLN(F("ERROR: Invalid key"));
      }
      break;
    case '0':
      DEBUG_PRINTLN(F("Operational mode"));
      return; // jump out of loop, start software
      break;
    case 'r':
    case 'R':
      DEBUG_PRINT(F("Are you sure? (y/n): "));
      len = inputReadline(buf, serialBuflen);
      if (len == 1 && (buf[0] == 'Y' || buf[0] == 'y'))
      {
        configInit(); // everything to 0, DevEUI reset
      }
      else
      {
        DEBUG_PRINTLN(F("Invalid input... abort"));
      }
      break;
    default:
      DEBUG_PRINTLN(F("Unknown"));
      menuPrint();
    }
  }
}

// 4) Flower functioning
void Read_battery()
{ 
  //voltage, *2 because of voltage devider, calibration value set at 1.005797 with multimeter
  //measured voltage at VCC pin 3.27 V (not exactly 3.3 V)
  Battery_voltage = analogRead(Battery_pin) * 2 * (3.27 / 1024) * 1.005797;

  if (Battery_voltage >= WARNING_VOLTAGE)
  {
    batteryWarning = 0; //normal function
  }
  if (Battery_voltage < WARNING_VOLTAGE)
  {
    batteryWarning = 1; //warning: battery low
  }
}

void refill()
{
  myServo.attach(servoControl);
  digitalWrite(PowerSwitch, LOW); //power switch ON
  DEBUG_PRINTLN(F(" -> REFILL"));
  myServo.write(SERVO_OPEN, SERVO_SPEED, true);  //position = open, slow speed, true = wait until position reached
  delay(REFILL_TIME);                            // keep servo arm in nectar reservoir
  myServo.write(SERVO_CLOSE, SERVO_SPEED, true); //position = close
  digitalWrite(PowerSwitch, HIGH);               //power switch OFF
  myServo.detach();                              //to save energy

  startTimeAutoRefill = millis();
}

void automaticRefill()
{
  //if (millis() >= startTimeAutoRefill + AUTO_REFILL_TIME)
  if ((millis() - startTimeAutoRefill)/1000 >= refillGap)
  {
    DEBUG_PRINT(F("Automatic")); //dev.
    refill();
  }
}

void Battery_LEDflash(unsigned long normalInterval, unsigned long warningInterval)
{
  Read_battery();
  currentBatteryTime = millis();
  if (DEV_MODE == true) //development
  {
    if (batteryWarning == 0)
    {
      if (currentBatteryTime >= LightTimer + normalInterval and currentBatteryTime <= LightTimer + normalInterval + FLASH_TIME)
      {
        digitalWrite(PowerSwitch, LOW); // ON
        FastLED.setBrightness(20);
        leds[0] = CRGB::Green;
        FastLED.show();
      }

      if (currentBatteryTime > LightTimer + normalInterval + FLASH_TIME)
      {
        leds[0] = CRGB::Black;
        FastLED.show();
        digitalWrite(PowerSwitch, HIGH); // OFF
        LightTimer = millis();
      }
    }

    if (batteryWarning == 1) // flashing to show battery low
    {
      if (currentBatteryTime >= LightTimer + warningInterval)
      {
        digitalWrite(PowerSwitch, LOW); // ON
        FastLED.setBrightness(20);
        leds[0] = CRGB::Red;
        FastLED.show();
      }

      if (currentBatteryTime >= LightTimer + warningInterval + FLASH_TIME)
      {
        leds[0] = CRGB::Black;
        FastLED.show();
        digitalWrite(PowerSwitch, HIGH); // OFF
        LightTimer = millis();
      }
    }
  }
}

void savetoRAM(unsigned long startTime, uint8_t visitDuration)
{
  if (DEV_MODE == true) //development
  {
    digitalWrite(PowerSwitch, LOW); // ON
    FastLED.setBrightness(50);
    leds[0] = CRGB::SkyBlue;
    FastLED.show();
    delay(50);
  }

  if (visitDuration > 0)
  { //only save when visit duration at least 1 sec.
    visitRec element;
    element.startVisit = startTime; //in sec.
    element.visit = visitDuration;  //in sec.
    if (!visitQueue.push(&element)) // add visit to queue -> 'first in first out' principle
    {
      //if false: queue is full, too many visits
      queueIsFull = 1;
      DEBUG_PRINT(F("ERROR: memory full"));
    }

    else
    {
      DEBUG_PRINTLN(F(" -> SAVED"));
      DEBUG_PRINTLN(F(""));
      queueIsFull = 0;
    }
  }

  leds[0] = CRGB::Black;           //development
  FastLED.show();                  //development
  digitalWrite(PowerSwitch, HIGH); // OFF //development
}
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
void loop()
{
  //1. Going-To-Sleep State
  if (FlowerState == goingToSleep)
  {
    DEBUG_PRINTLN(F(""));
    DEBUG_PRINTLN(F("GOING TO SLEEP"));

    visitState = 0;

    digitalWrite(PowerSwitch, HIGH); //power switch OFF
    digitalWrite(IRemitterPower, LOW);
    digitalWrite(IRreceiverPower, LOW);

    while (!visitQueue.isEmpty())
    { //send data untill queue is empty
      sendData(GOING_TO_SLEEP_SEND_FREQUENCY, 1); // send data over LoRaWAN, port 1
    }

    DEBUG_PRINTLN(F(""));
    DEBUG_PRINTLN(F("SLEEP"));
    
    reconnectNeed = true;

    FlowerState = sleep;

  } // goingToSleep state end

  //2. Sleep State
  if (FlowerState == sleep)
  {   
    // deep sleep mode

    while (sleepCounter < SLEEP_TIME)
    { // deep sleep for some time during night to save battery
      sleepCounter += 8;

      if (DEV_MODE == true && DEV_SLEEP_MODE == true)
      { //keep serial monitor open for development
        delay(7000);

        digitalWrite(PowerSwitch, LOW); // ON
        FastLED.setBrightness(50);
        leds[0] = CRGB::BlueViolet;
        FastLED.show();
        delay(1000);
        digitalWrite(PowerSwitch, HIGH); // OFF

        DEBUG_PRINT(F("Deep Sleep:"));
        DEBUG_PRINT(sleepCounter);
        DEBUG_PRINT(F("/"));
        DEBUG_PRINTLN(SLEEP_TIME);
      }

      else
      { //.powerDown shuts down serial monitor (energy saving)
        if (DEV_MODE == true)
        { // flash led to signal sleep state
          digitalWrite(PowerSwitch, LOW); // ON
          FastLED.setBrightness(50);
          leds[0] = CRGB::BlueViolet;
          FastLED.show();
          delay(1000);
          digitalWrite(PowerSwitch, HIGH); // OFF
        }

        LowPower.powerDown(SLEEP_8S, ADC_OFF, BOD_OFF); //max. sleep time 8 sec. (+- 10%)
      }
    }

    //interupt sleep to send message now and then to be able to receive message with LoRaWAN
    if (reconnectNeed == true)
    {//connect LORaWAN - Try to join the network
      LoRaConnect();
    }

    if (DEV_MODE == true && DEV_SLEEP_MODE == true)
    { //keep serial monitor open for development
      sendData(SLEEP_SEND_FREQUENCY_DEV, 2); // send data over LoRaWAN, port 2
      delay(8000);
    }

    else
    { 
      sendData(SLEEP_SEND_FREQUENCY,2); //send to be able to receive message for waking up, port 2
    }

    if (timeToSleep == false) //Go to wake-up when message received through LoRaWAN tells it's time to do so
    {
      FlowerState = wakeUp;
    }

  } // sleep state end

  //3. Wake-Up State
  if (FlowerState == wakeUp)
  {
    sleepCounter = 0; // reset

    DEBUG_PRINTLN(F(""));
    DEBUG_PRINTLN(F("WAKE UP"));

    startTimeAutoRefill = millis(); //start automatic refill timer
    sendStartTime = millis();       //start timer for message sending
    LightTimer = millis();          // start timer for flashing

    //first IR-sensor read - to start
    digitalWrite(IRreceiverPower, HIGH);
    delay(1);
    digitalWrite(IRemitterPower, HIGH);
    delay(20);
    previousSensorValue = analogRead(IRsensorRead);
    
    digitalWrite(IRreceiverPower, LOW);
    digitalWrite(IRemitterPower, LOW);

    DEBUG_PRINTLN(F(""));
    DEBUG_PRINTLN(F("WORK"));

    FlowerState = work;
  } // wake-up state end

  //4. Work State
  if (FlowerState == work)
  {
    if (timeToSleep == true)
    { //Go to sleep when message received through LoRaWAN tells it's time to do so
      FlowerState = goingToSleep;
    }

    Battery_LEDflash(NORMAL_FLASH_INTERVAL, WARNING_FLASH_INTERVAL); // flash led to show functioning (development only)
    sendData(WORK_SEND_FREQUENCY, 1);   // send data over LoRaWAN (e.g. every 10min.), port 1
    automaticRefill();                  // automatic servo movement to prevent drying out of nectar

    // detection system timer reset
    if (millis() > startTimeCycle + CYCLE_TIME)
    {
      startTimeCycle = millis();
    }

    //check if reconnecting is needed
    if (failedToSendCount >= RECONNECTION_TRESHOLD)
    {
      LoRaConnect();
      failedToSendCount = 0; // reset
    }

    // detection on
    if (millis() <= startTimeCycle + ON_TIME)
    {
      //IR-sensor system turned on once every TimeCycle
      digitalWrite(IRreceiverPower, HIGH);
      delay(1);
      digitalWrite(IRemitterPower, HIGH);
      delay(1);
      sensorValue = analogRead(IRsensorRead); //read voltage of IR sensor
      delay(1);
      digitalWrite(IRemitterPower, LOW);
      digitalWrite(IRreceiverPower, LOW);
  
      

      if (SHOW_VALUE == true) //development
      {
        DEBUG_PRINT(F("IR:")); DEBUG_PRINTLN(sensorValue);
        //DEBUG_PRINT(F("Previous value: ")); DEBUG_PRINTLN(previousSensorValue);
        //DEBUG_PRINT(F("Battery: "));DEBUG_PRINT(Battery_voltage); DEBUG_PRINTLN(F("v"));
        //DEBUG_PRINT(F("Warning: ")); DEBUG_PRINTLN(batteryWarning); DEBUG_PRINTLN(F(""));
        //DEBUG_PRINT((millis() - refillGapTimer)/1000); DEBUG_PRINT(" / "); DEBUG_PRINT(refillGap); DEBUG_PRINT(" - Refill need: "); DEBUG_PRINTLN(refillNeed);
      }

      // visit
      if (sensorValue <= previousSensorValue - SENSOR_SENSITIVITY)
      {
        if (DEV_MODE == true)
        {
          digitalWrite(PowerSwitch, LOW); // ON
          FastLED.setBrightness(50);
          leds[0] = CRGB::Red;
          FastLED.show();
        }

        if (visitState == 0)
        { //new visit starting
          startVisit = round(millis()) / PRECISION;
          startVisitTimer = millis();
        }

        // max duration of 250 sec; because of rounding, visits less then 0,5 sec. are not registered (=0)
        visitCounter = round((millis() - startVisitTimer) / PRECISION); 

        visitState = 1;
        previousVisitState = 1;

        // max visit time reached
        if (visitCounter >= MAX_VISIT_DURATION) //maxCounter not over 255 (to be able to send visitDuration in 1 byte)
        { // visitor might be sleeping (or dead) in flower

          DEBUG_PRINTLN(F("Max.visit")); //dev.
          //DEBUG_PRINT(visitCounter); DEBUG_PRINTLN(F("sec."));

          savetoRAM(startVisit, visitCounter); //save visit start time & visit duration

          visitState = 0;
          previousVisitState = 0;

          obstrCounter++;
          if (obstrCounter >= OBSTR_TRESH)
          {
            obstruction = 1;
          }
        }

        LightTimer = millis();          //development, avoid LED flashing during visit
      }

      // no visit
      else
      {
        visitState = 0;
        previousSensorValue = sensorValue;
        obstruction = 0; //reset

        //shut down LED when it was switched on in development mode
        leds[0] = CRGB::Black;
        FastLED.show();
        digitalWrite(PowerSwitch, HIGH); // OFF
      }

      // end of visit
      if (previousVisitState != visitState)
      {
        DEBUG_PRINTLN(F(""));
        DEBUG_PRINT(F("Visit: "));
        DEBUG_PRINT(visitCounter);
        DEBUG_PRINT(F(" sec."));

        savetoRAM(startVisit, visitCounter); //save start time & visit duration to queue

        visitCounter = 0;
      }

      previousVisitState = visitState;

      delay(100); // check if cycle has passed every 10 times per second in stead of constant, save energy
      
    }
  } // work state end
}

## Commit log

2021-10-15 Create File Logger Flow (JSON)
2021-10-15 Create Flower Flow (JSON)
2021-10-15 Rename File Logger Flow (JSON) to NodeRed - File Logger Flow (JSON)
2021-10-15 Rename Flower Flow (JSON) to Node-RED Flower Flow (JSON)
2021-10-15 Rename NodeRed - File Logger Flow (JSON) to Node-RED - File Logger Flow (JSON)
2021-10-18 Rename Node-RED - File Logger Flow (JSON) to Node-RED/File Logger Flow (JSON)
2021-10-18 Rename Node-RED Flower Flow (JSON) to Node-RED/Flower Flow (JSON)
2021-11-29 Update Flower Flow (JSON)
